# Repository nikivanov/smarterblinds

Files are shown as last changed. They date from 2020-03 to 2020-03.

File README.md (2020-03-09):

# Overview
<p align="center">
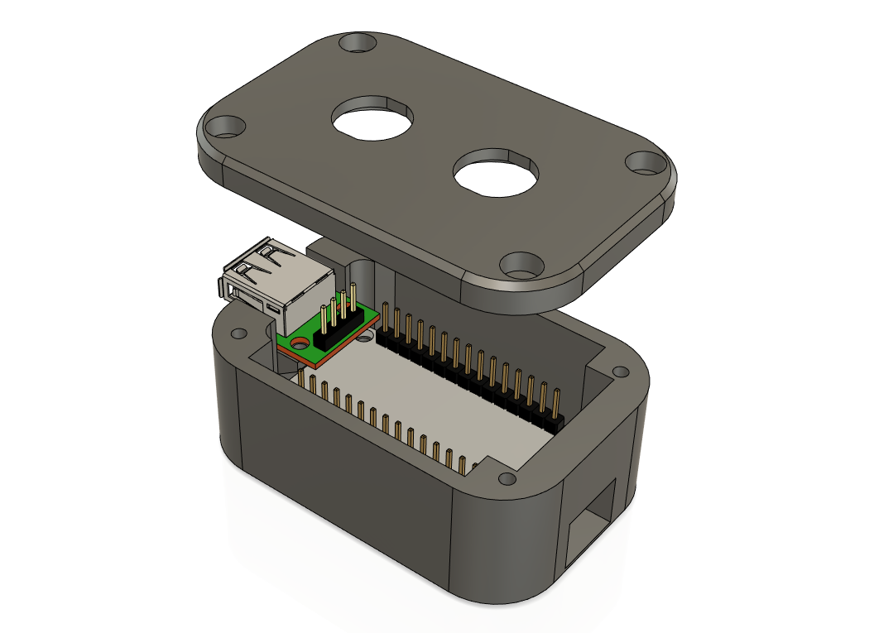
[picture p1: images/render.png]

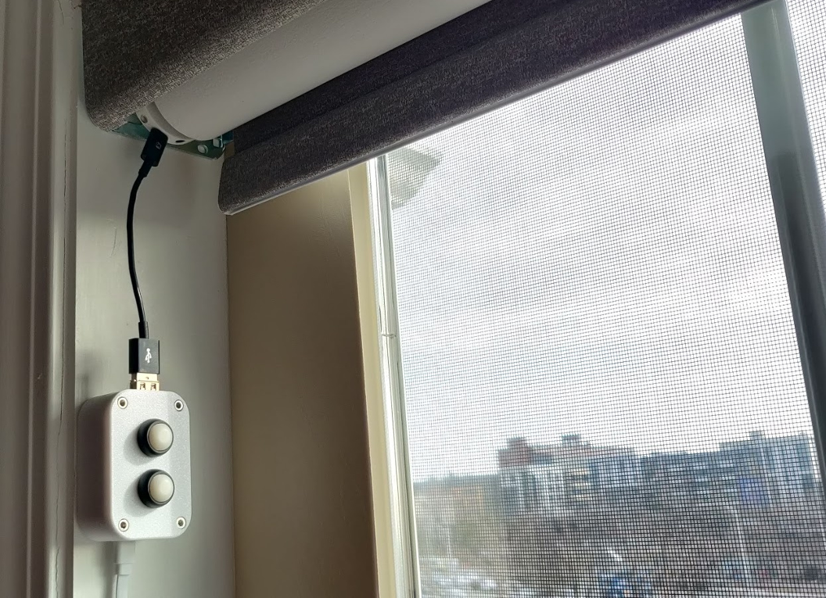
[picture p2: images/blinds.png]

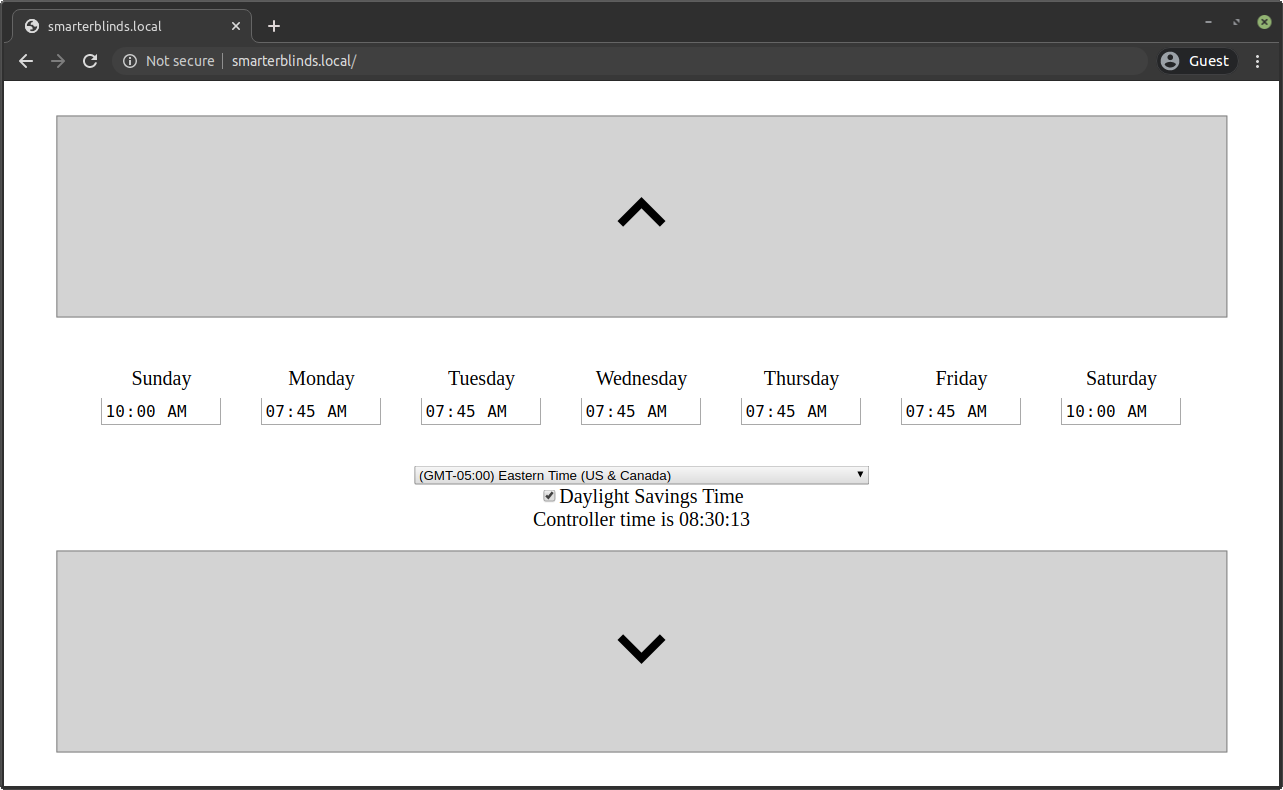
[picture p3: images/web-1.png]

</p>
Blinds-To-Go sells motorized roller blinds controllable via a wand with two buttons, which connects to the blinds over Micro-USB. Unfortunately, it does not offer any smart functionality, but having a Micro-USB connection makes it very hackable. Hooking up the wand to a breakout board shows that Up and Down buttons short D+ / D- pins to ground. This project replaces the wand with an ESP8266 microcontroller to allow raising blinds on schedule as well as remote control via the phone / browser. 

I'm not associated with Blinds-To-Go and I'm not responsible for any damage caused to or by your blinds. With that being said, hack away!

# Description
Once you flash your microcontroller with the provided code and plug it in, it will:
* Attempt to connect to WiFi. If this is the first time you're starting it up, or if the existing WiFi configuration is no longer valid, it will host an unsecure SmarterBlinds WiFi hotspot. Connect to it via your phone, go through captive portal and connect it to your WiFi.
* Once WiFi is connected, the controller will start an mDNS service so you can access it at http://smarterblinds.local If you don't have mDNS, you'll have to figure out the assigned IP from your router.
* The web page has simple up and down controls to mimic the wand button behavior - you have to press and hold the buttons for about a second for the blinds to go up or down. The web page also allows you to set a time for each day to raise the blinds to the `Favorite 1` position (the position when you double-click the Up button).
* You need to set your time offset and DST setting. Refresh the page to verify that controller time matches your clock.
* ESP8266 does not have a real time clock, but since we have WiFi we can keep time using NTP. This allows the controller to match current time against the specified schedule.
* ESP8266 needs constant USB power. The good news is that it will also keep your blinds fully charged.

# Ingredients
* [NodeMCU ESP8266 board](images/nodemcu.jpg)
* [USB Type A breakout board](images/breakout_board.jpg)
* [2x 12mm Waterproof Momentary N.O. Push Button Switch](images/buttons.jpg)
* 10x M3 6mm bolts

# Setup
* In the `stls` folder, you'll find a case that will fit an ESP8266 board, a USB breakout board and 2 buttons. It can be 3D printed without supports. 
* At the top of the Arduino sketch, you can see (and change, if you'd like) the pins in use:
    ```
    #define UP_PIN 4
    #define DOWN_PIN 5
    #define BUTTON_UP_PIN 12
    #define BUTTON_DOWN_PIN 14
    ```
* Solder the pins to the USB breakout board as follows:
    * UP_PIN to D+
    * DOWN_PIN to D-
    * Vin to VBus
    * Gnd to Gnd
* Solder the buttons to the pins as follows (polarity doesn't matter):
    * Up Button to BUTTON_UP_PIN
    * Down Button to BUTTON_DOWN_PIN
    * Other contact of each button can be soldered together and then soldered to GND.
* Test everything first, and if all is well, secure everything with M3 bolts.

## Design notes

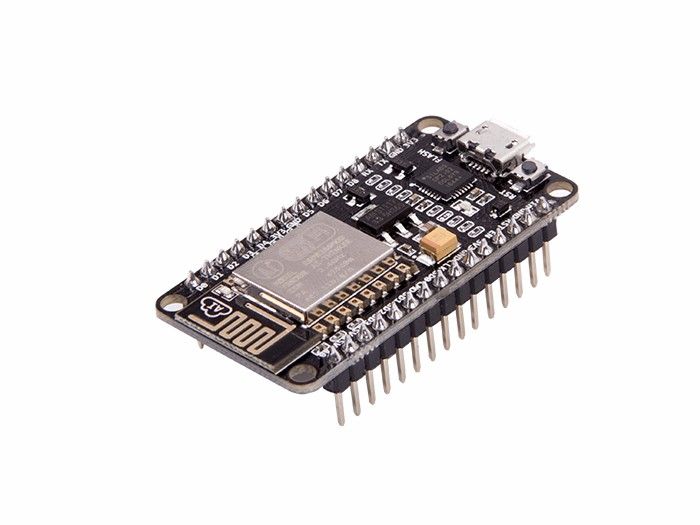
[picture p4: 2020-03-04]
images/nodemcu.jpg

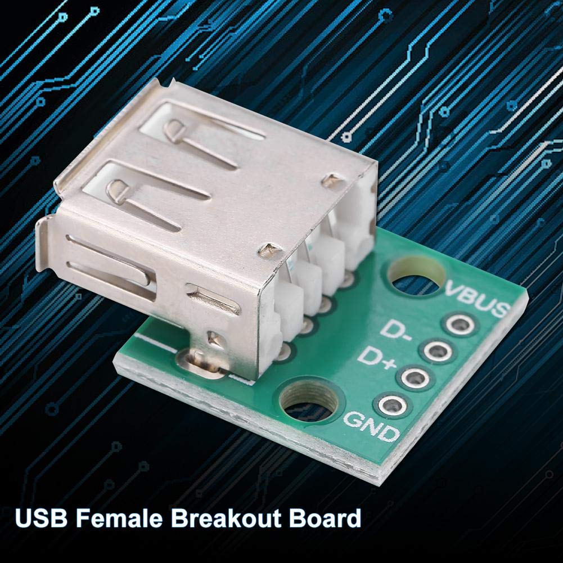
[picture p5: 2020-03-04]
images/breakout_board.jpg

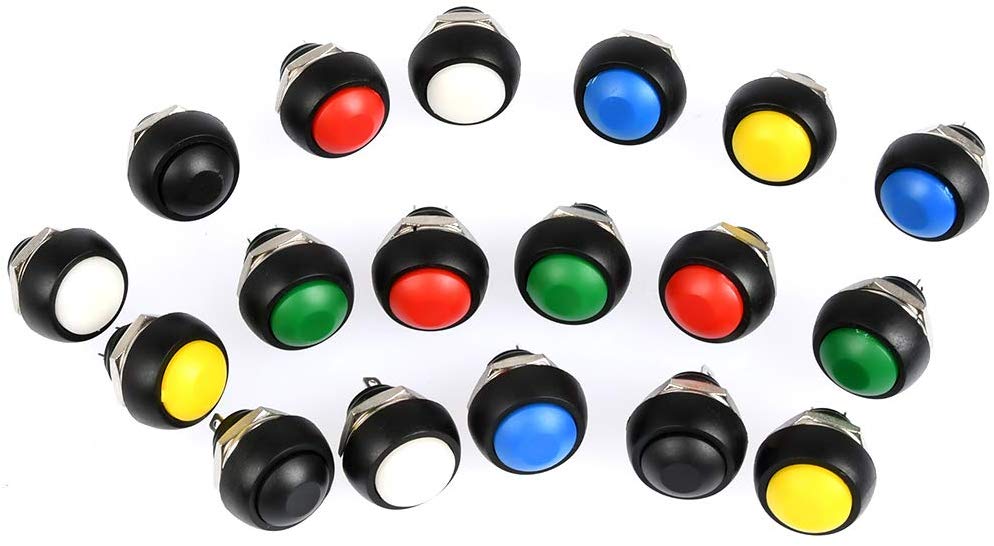
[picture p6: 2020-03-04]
images/buttons.jpg

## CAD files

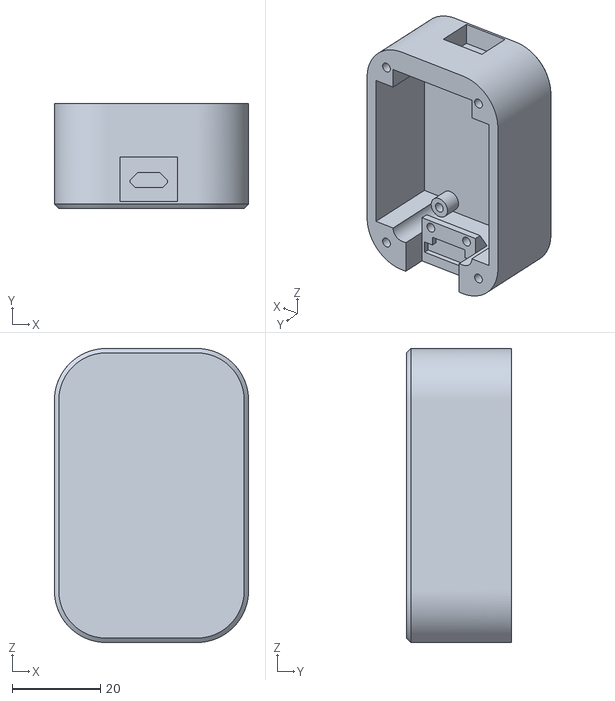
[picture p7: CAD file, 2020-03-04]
stls/case.stl
44.0 x 23.8 x 66.7

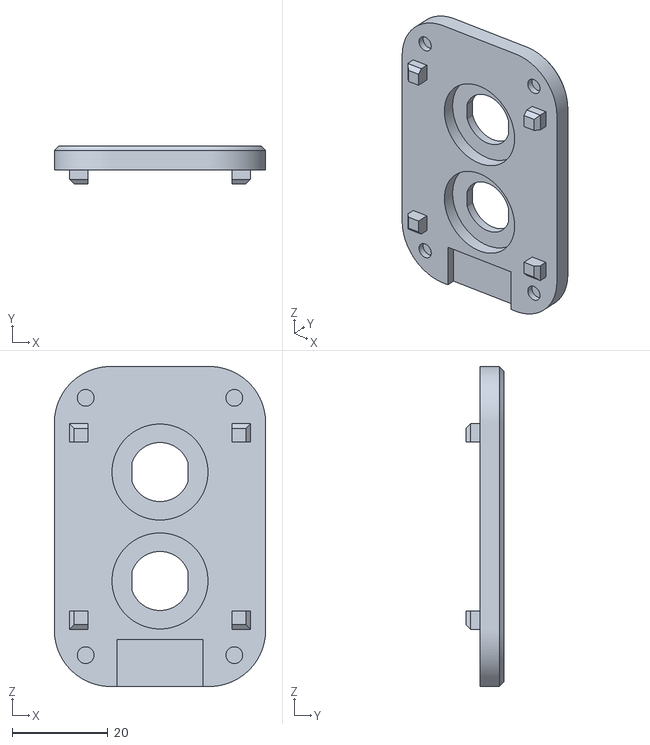
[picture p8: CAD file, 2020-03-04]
stls/cover.stl
44.0 x 8.00 x 66.7

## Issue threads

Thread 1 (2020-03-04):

ESP and USB breakout boards used in the project are not specified in README

alsii, 2020-03-04:
There are many  different kinds of  ESP boards on the market. Which one have you designed the case for?

nikivanov, 2020-03-04:
Added BOM with images. Thanks!

Closed 2020-03-04.

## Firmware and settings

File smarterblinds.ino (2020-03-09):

#include <ArduinoJson.h>
#include <ESP8266mDNS.h>
#include <ESP8266WiFi.h>
#include <DNSServer.h>            //Local DNS Server used for redirecting all requests to the configuration portal
#include <ESP8266WebServer.h>     //Local WebServer used to serve the configuration portal
#include <WiFiManager.h>
#include <WiFiClient.h>
#include <NTPClient.h>
#include <FS.h>

#define UP_PIN 4
#define DOWN_PIN 5
#define BUTTON_UP_PIN 12
#define BUTTON_DOWN_PIN 14

WiFiUDP ntpUDP;
NTPClient timeClient(ntpUDP);
DynamicJsonDocument config(1024);
ESP8266WebServer server(80);

void setup() {
  pinMode(UP_PIN, OUTPUT);
  pinMode(DOWN_PIN, OUTPUT);
  digitalWrite(UP_PIN, HIGH);
  digitalWrite(DOWN_PIN, HIGH);
  pinMode(BUTTON_UP_PIN, INPUT_PULLUP);
  pinMode(BUTTON_DOWN_PIN, INPUT_PULLUP);

  delay(10);
  Serial.begin(115200);

  if(!SPIFFS.begin()){
    Serial.println("An Error has occurred while mounting SPIFFS");
    return;
  }

  Serial.println("Starting WiFi manager");

  WiFiManager wifiManager;
  wifiManager.autoConnect("SmarterBlinds");

  Serial.println("Connected to WiFi");
  Serial.println("Starting mDNS");

  if (MDNS.begin("smarterblinds")) {
    Serial.println("mDNS responder started");  
  }
  
  timeClient.begin();
  Serial.println("NTP client started");

  File configFile = SPIFFS.open("/config.txt", "r");
  if (configFile) {
    Serial.println("Config file found");
    deserializeJson(config, configFile);
    configFile.close();
    initTimeClientFromConfig();
  }

  server.on("/", handleRoot);
  server.on("/index.html", handleRoot);
  server.on("/blinds.js", handleJS);
  server.on("/blinds.css", handleCSS);
  server.on("/settings", handleSettings);
  server.on("/up", handleUp);
  server.on("/down", handleDown);
  
  server.begin();
  
  Serial.println("Server started");
}

void initTimeClientFromConfig() {
  int offsetHours = config["offsetHours"].as<int>();
  bool dst = config["dst"].as<bool>();
  if (dst) {
    offsetHours = offsetHours + 1;
  }
  int offsetSeconds = offsetHours * 60 * 60;
  timeClient.setTimeOffset(offsetSeconds);
}

int desiredDirection = 0;
int lastDirection = 0;
bool upLatched = false;
bool downLatched = false;
void loop(void) {
  desiredDirection = 0;
  timeClient.update();

  MDNS.update();

  server.handleClient();
  
  int upButtonVal = digitalRead(BUTTON_UP_PIN);
  int downButtonVal = digitalRead(BUTTON_DOWN_PIN);

  if (upButtonVal == LOW || upLatched) {
    desiredDirection = 1;
  }

  if (downButtonVal == LOW || downLatched) {
    desiredDirection = -1;
  }

  if (desiredDirection != lastDirection) {
    Serial.println(String("New direction ") + desiredDirection + " last direction " + lastDirection);
    if (desiredDirection == 0) {
      digitalWrite(UP_PIN, HIGH);
      digitalWrite(DOWN_PIN, HIGH);
    } else if (desiredDirection == 1) {
      digitalWrite(UP_PIN, LOW);
      digitalWrite(DOWN_PIN, HIGH);
    } else if (desiredDirection == -1) {
      digitalWrite(UP_PIN, HIGH);
      digitalWrite(DOWN_PIN, LOW);
    } 
    delay(100); 
  }

  lastDirection = desiredDirection;
  checkSchedule();
}

char daysOfTheWeek[7][12] = {"Sunday", "Monday", "Tuesday", "Wednesday", "Thursday", "Friday", "Saturday"};
void checkSchedule() {
  const char* currentDoW = daysOfTheWeek[timeClient.getDay()];
  if (config["schedule"][currentDoW] != NULL) {
    //Serial.println(String(currentDoW) + " " + timeClient.getHours() + " " + timeClient.getMinutes() + " " + String(config["schedule"][currentDoW]["localHours"].as<int>()) + " " + String(config["schedule"][currentDoW]["localMinutes"].as<int>()));
    if (timeClient.getHours() == config["schedule"][currentDoW]["localHours"].as<int>()) {
      if (timeClient.getMinutes() == config["schedule"][currentDoW]["localMinutes"].as<int>()) {
        if (timeClient.getSeconds() >= 0 && timeClient.getSeconds() <= 2) {
          Serial.println("Schedule match");
          digitalWrite(UP_PIN, LOW);
          delay(100);
          digitalWrite(UP_PIN, HIGH);
          delay(100);
          digitalWrite(UP_PIN, LOW);
          delay(100);
          digitalWrite(UP_PIN, HIGH);
          delay(100);

          delay(3000);
        }
      }
    }
  }
}

void handleSettings() {
  Serial.println("Settings");
  if (server.method() == HTTP_POST) {
    Serial.println("Got settings from browser");
    Serial.println(server.arg("plain"));
    File configFile = SPIFFS.open("/config.txt", "w");
    configFile.print(server.arg("plain"));
    deserializeJson(config, server.arg("plain"));
    configFile.close();
    initTimeClientFromConfig();
    server.send(200, "text/plain", "OK");
  }
  else if (server.method() == HTTP_GET) {
    Serial.println("Sent settings to the browser");
    String output;
    Serial.println("Sending currentTimeMS " + timeClient.getFormattedTime());
    DynamicJsonDocument configCopy(1024);
    configCopy = config;
    configCopy["currentTime"] = timeClient.getFormattedTime();
    serializeJson(configCopy, output);
    server.send(200, "text/json", output);
    Serial.println(output);
  }
}

void handleUp() {
  bool pressed = server.arg(0) == "true"; 
  if (pressed) {
    desiredDirection = 1;
    upLatched = true;
  } else {
    desiredDirection = 0;
    upLatched = false;
  }
  server.send(200, "text/plain", "OK");
}

void handleDown() {
  bool pressed = server.arg(0) == "true"; 
  if (pressed) {
    desiredDirection = -1;
    downLatched = true;
  } else {
    desiredDirection = 0;
    downLatched = false;
  }
  server.send(200, "text/plain", "OK");
}

void handleRoot() {
  handleFileRead("/index.html");
}

void handleJS() {
  handleFileRead("/blinds.js");
}

void handleCSS() {
  handleFileRead("/blinds.css");
}

String getContentType(String filename) { // convert the file extension to the MIME type
  if (filename.endsWith(".html")) return "text/html";
  else if (filename.endsWith(".css")) return "text/css";
  else if (filename.endsWith(".js")) return "application/javascript";
  else if (filename.endsWith(".ico")) return "image/x-icon";
  return "text/plain";
}

bool handleFileRead(String path) { // send the right file to the client (if it exists)
  Serial.println("handleFileRead: " + path);
  if (path.endsWith("/")) path += "index.html";         // If a folder is requested, send the index file
  String contentType = getContentType(path);            // Get the MIME type
  if (SPIFFS.exists(path)) {                           // If the file exists
    File file = SPIFFS.open(path, "r");                 // Open it
    size_t sent = server.streamFile(file, contentType); // And send it to the client
    file.close();                                       // Then close the file again
    return true;
  }
  Serial.println("\tFile Not Found");
  return false;                                         // If the file doesn't exist, return false
}
